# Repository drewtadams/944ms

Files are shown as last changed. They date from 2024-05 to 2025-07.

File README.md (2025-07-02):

# 944ms

The purpose of this guide is to walk through the microsquirt conversion process on an early Porsche 944 with the following goals in mind:

1. utilize as many of the stock parts as possible
2. avoid or minimize the amount of non-bolt-on modifications and fabrication
3. for any part that must be fabricated, try to do so in a way that is easily or readily available (e.g. 3d printing)

**Please read the [DISCLAIMER](disclaimer) before proceeding with any modifications.**

## Sections

 1. [Useful Links](#useful-links)
 2. [Printed Parts](#printed-parts)
 3. [Required Parts](#required-parts)
 4. [Putting it Together](#putting-it-together)

## Useful Links

Though detailed instructions of the entire build can be found in the [Putting it Together](#putting-it-together) section, there are several forums, guides, documentation, and general conversations that were researched and poured over for this project. The information found has proven invaluable and could prove beneficial for other MicroSquirt conversions. They are listed below:

 * [Microsquirt setup/use guide](https://www.useasydocs.com/) (note the [wiring diagram](https://www.useasydocs.com/details/ew3_hires.gif))
 * [General build](https://rennlist.com/forums/924-931-944-951-968-forum/873173-summer-build-thread-megasquirt-and-more-2.html)
 * [General parts overview and tune settings](https://rennlist.com/forums/924-931-944-951-968-forum/831248-a-practical-guide-to-megasquirting-your-944-a.html)
 * [General discussion](https://rennlist.com/forums/924-931-944-951-968-forum/860305-who-is-using-microsquirt-megasquirt.html)
 * Hall sensor on cam: [msextra](https://www.msextra.com/forums/viewtopic.php?t=69564) and [rennlist](https://rennlist.com/forums/944-turbo-and-turbo-s-forum/1088676-fyi-crank-trigger-solution-for-30-no-trigger-wheel-needed.html)
 * [Generic wiring guide](https://rennlist.com/forums/924-931-944-951-968-forum/424355-microsquirt-stand-alone-ecu-installation-guide.html) (particularly useful when used in conjunction with the [speed/reference sensor pinout](https://www.clarks-garage.com/shop-manual/ign-02.htm) for connecting hall sensor to VR-1 or VR-1)
 * [Youtube wiring playlist](https://www.youtube.com/playlist?list=PL6KUN7OA-UQNufmcnJdhSTtK0emy2OQQv)
 * General build checklist: [reddit](https://www.reddit.com/r/megasquirt/comments/3fw4x1/porsche_944_microsquirt_project_completed/) or [msextra](https://www.msextra.com/forums/viewtopic.php?t=59524)
 * TPS alternatives: [951](https://rennlist.com/forums/944-turbo-and-turbo-s-forum/1267168-951-throttle-position-sensor-tps-alternative-solution.html) or [m50](https://rennlist.com/forums/944-turbo-and-turbo-s-forum/968375-what-alternate-tps-units-fit-our-throttle-bodies-2.html)
 * [Alternative VW parts](https://m.me/ch/AbbR2fU9JG5es8ac/)
 * Interchangable parts: [google docs](https://docs.google.com/spreadsheets/d/1jSTkPCnTwhv91jEnysElxuuS8_pDJxy0), [deancent.com](https://www.deancent.com/porsche-944-parts-without-the-premium-price-tag/), or [rennlist](https://rennlist.com/forums/924-931-944-951-968-forum/297421-parts-cross-reference.html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)
 * [DME plug swap](https://rennlist.com/forums/944-and-944s-forum/1266575-microsquirt-ecu-for-porsche-944-s2-motronic-replacement-how-to.html)
 * [Clark's Garage](https://www.clarks-garage.com/) (voltages, current ratings, etc.)

## Printed Parts

All parts were designed to be printed on an Ender 5+ and sliced with Cura. Some adjustments may be necessary depending on the printer and/or slicer, either to the .stl or the printed part itself (e.g. drilling, filing, or sanding down some areas), but general dimensions should be close enough to work. While the links below direct to Thingiverse, the .stl files have also been included under `/printed_parts`.

 * [AFM mods](https://www.thingiverse.com/thing:6618742)
 * [IAT intake tube](https://www.thingiverse.com/thing:6598815)
 * [m50 TPS adapter](https://www.thingiverse.com/thing:6610332)

> Note: the AFM mods and TPS adapter were eventually sent to be machined by a 3rd party service ([SendCutSend](https://sendcutsend.com/)) in 6061 T6 aluminum. While certain plastics likely would have worked well, I opted for a more rigid and heat-tolerant material. They totalled roughly $25.

## Required Parts

The following parts are what were chosen based on price, shipping times, ease of install, or a combination of the aforementioned. Additional parts that were considered but not used are listed [here](#additional-parts-considered). Some parts were purchased in multiples or bulk (e.g. fuses) because it was cheaper or nearly the same price to do so.

It should be noted that the total cost includes taxes and shipping midway through 2024; prices may be different depending on location, availability, and other miscellaneous factors (e.g. inflation, price hikes, etc.).

| Group | Item | Part Number | Price |
|---|---|---|---|
| Cam Sync | [Hall speed sensor](https://www.mouser.com/ProductDetail/ZF/GS100502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) | 540-GS100502 | `$45.05` |
| Cam Sync | [Flanged sleeve bearing](https://www.mcmaster.com/) | 7815K62 | `$12.59` |
| Cam Sync | [M12 x 1.00 tap](https://www.amazon.com/gp/product/B09X7HYMFM) | M12X1.0_Hand_Tap_RH | `$12.87` |
| Cam Sync | [2.4k ohm resistor](https://www.amazon.com/EDGELEC-Resistor-Tolerance-Resistance-Optional/dp/B07HDFRYPK) | B07HDFRYPK | `$5.89` |
| ECU | [MicroSquirt with 8' harness](https://www.diyautotune.com/product/microsquirt-engine-management-system-w-8-foot-wiring-harness/) | MicroSqrt8 | `$390.95` |
| ECU | [18"x8" aluminum sheet metal](https://www.acehardware.com/departments/hardware/metal-sheets-and-rods/sheet-metal/5157615) | 5157615 | `$12.99` |
| ECU | [48-position PDC with Terminal Seals](https://www.kinnettickreations.com/product-page/48-position-pdc) | NA | `$55.00` |
| ECU | [2x 4-pin High Capacity Relay](https://www.kinnettickreations.com/product-page/4-pin-high-capacity-iso-280-relay) | NA | `$10.00` |
| ECU | [Mini fuse kit](https://www.amazon.com/dp/B0D5CZNPQW) | BXS001 | `$5.98` |
| ECU | [36A 6-position terminal block](https://www.amazon.com/dp/B0B24FZWPH) | TB-3506 | `$8.99` |
| Fuel | [4x 33# high-impedance fuel injectors](https://www.ebay.com/itm/266002307469) | 0280150431 | `$96.17` |
| Ignition | [8x Chevy Ignition Coil](https://www.amazon.com/dp/B07FV8C4KJ) (only need 4) | 12611424 | `$89.99` |
| Ignition | [2x LS Ignition Coil Bracket](https://www.amazon.com/dp/B0BBR26F6S) | 12558693 | `$26.99` |
| Intake | [GM IAT open-element sensor](https://www.diyautotune.com/product/gm-open-element-iat-sensor-with-pigtail/) | IATwPiggy | `$24.49` |
| MAP | [GM 1 bar MAP with pigtail](https://www.ebay.com/itm/324792585183) | 12223861 | `$17.17` |
| O2 | [Spartan 2 wideband with LSU 4.9](https://www.14point7.com/products/spartan-lambda-controller-2) (discont. use Spartan 3) | NA | `$125.00` |
| Speed Sensor | [3 pin Bosch EV1 connector](https://www.amazon.com/dp/B0D6Y4Z4FP) | 191972525B | `$11.39` |
| TPS | [m50 TPS](https://www.autozone.com/engine-management/throttle-position-sensor-tps/p/uro-throttle-position-sensor-tps-uro-017795/1323039_0_0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) | 13631721456 | `$55.81` |
| TPS | [2x m3x25 bolt with nut](https://www.amazon.com/gp/product/B0BPFXP2M9) | BXG-M3-400-0012 | `$25.68` |

**Total Parts Cost: `$1,021.61`**

## Additional Parts Considered

The following are parts that were considered but not used. The indices here correlate with those in the [required parts](#required-parts) section above, as does the structure and format, but the cost may or may not include taxes and shipping as they weren't actually purchased. Additional research should be done before purchasing anything listed here to ensure it will work for your application if you choose to alter your route.

 1. Cam sync
    * [hall speed sensor, digikey](https://www.digikey.com/en/products/detail/zf-electronics/GS100502/361998) | GS100502 | `$46.36`
    * [hall speed sensor, diyautotune](https://www.diyautotune.com/product/crankshaft-position-sensor-hall-effect-threaded-body/) | HallThreaded-K | `$102.99`
    * [camshaft trigger kit, clewett](https://www.clewett.com/index.php?main_page=product_info&cPath=59&products_id=306) | 1002-08 | `$195.00`
    * [camshaft trigger kit, lindsey racing](https://www.lindseyracing.com/LR/Porsche/LRA-EM-CAM-ASSY.html) | LRA-EM-CAM | `$475.00`
 2. MAP
    * [GM 1 bar MAP, amazon](https://www.amazon.com/AUTEX-Manifold-Absolute-Pressure-Compatible/dp/B0BB6J8PB2) | 19106672 | `$15.05`
    * [GM 1 bar MAP, clewett](https://www.clewett.com/index.php?main_page=product_info&products_id=80) | 71110 | `$61.00`
 3. [LS2 coil pack](https://thedubshop.com/ls2-coil-pack-set-import/) | IGN_COIL_LS2-IMP-SET
 | `$99.95`
 4. TPS
    * [951, ebay, used](https://www.ebay.com/itm/166226599785) | 280120400 | `$124.99`
    * [951, ebay, new](https://www.ebay.com/itm/362088697124) | 280120400 | `$244.97`
 5. [distributor delete plate](https://www.clewett.com/index.php?main_page=product_info&products_id=309) | 1002-06 | `$56.00`

## Putting it Together

### Cam sync

A general discussion for utilizing a hall effect sensor can be found on [rennlist](https://rennlist.com/forums/944-turbo-and-turbo-s-forum/1088676-fyi-crank-trigger-solution-for-30-no-trigger-wheel-needed.html). The process used here is similar, with the only difference being the orientation of the sleeve bearing.

As opposed to having the flange of the sleeve bearing on the outside of the cam timing belt cover:

 1. grind/sand down the protruding rib on the inside of the cover closest to the inspection hole and one side of the sleeve & flange
 2. press the sleeve bearing into the inspection hole from the inside with a rubber mallet and a large diameter punch or bold head

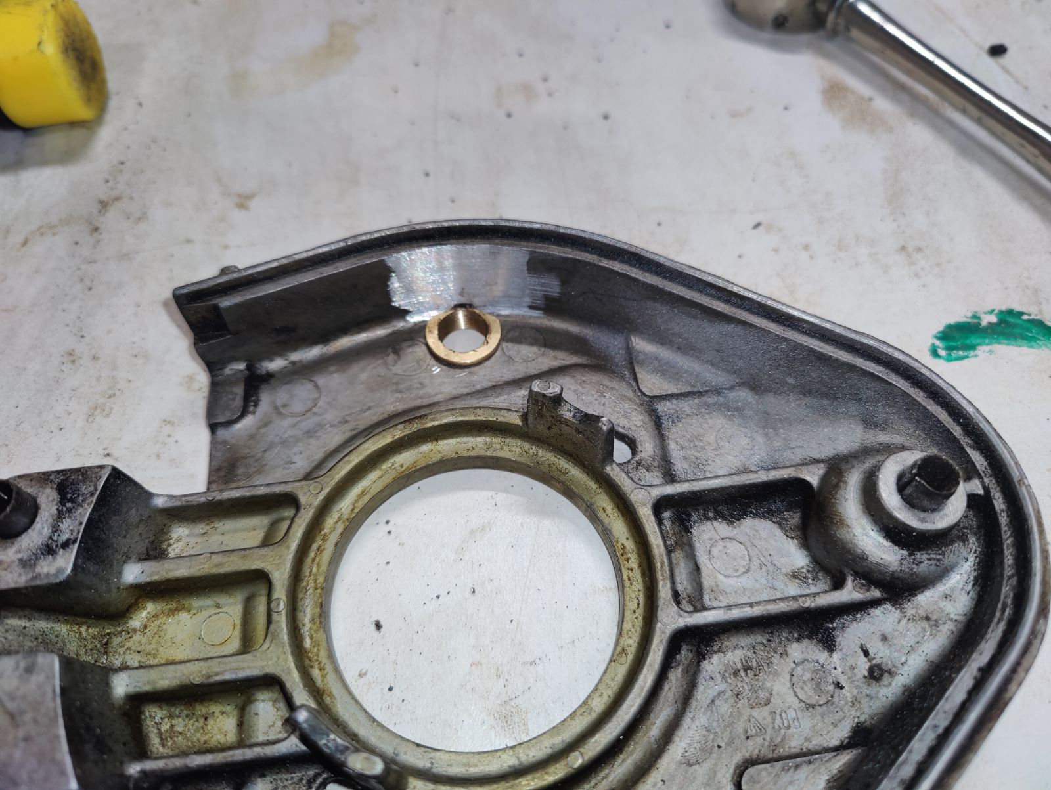
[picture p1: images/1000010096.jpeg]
ground and pressed sleeve bearing


3. grind off the protruding portion of the sleeve from the outside

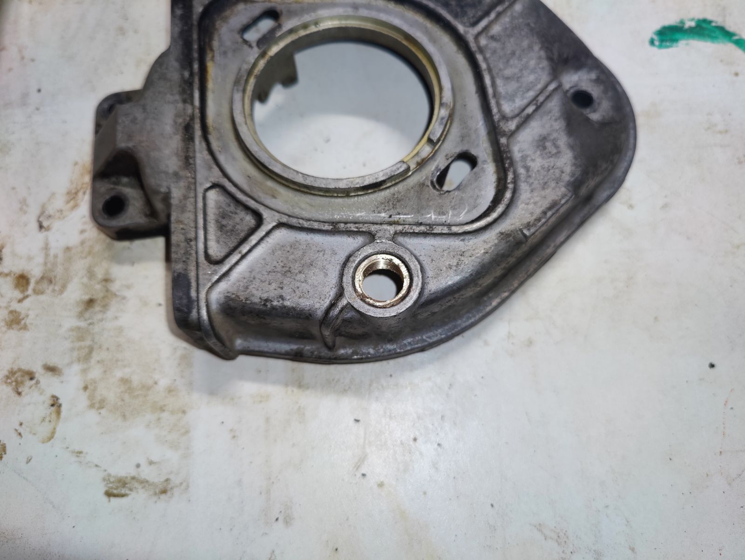
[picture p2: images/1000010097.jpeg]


4. clean up the grind and tap the sleeve with an m12x1mm tap

Once tapped, the hall effect sensor should be able to thread easily into the sleeve bearing. This method uses the flange to keep the sensor from backing out of the cover without relying on adhesives.

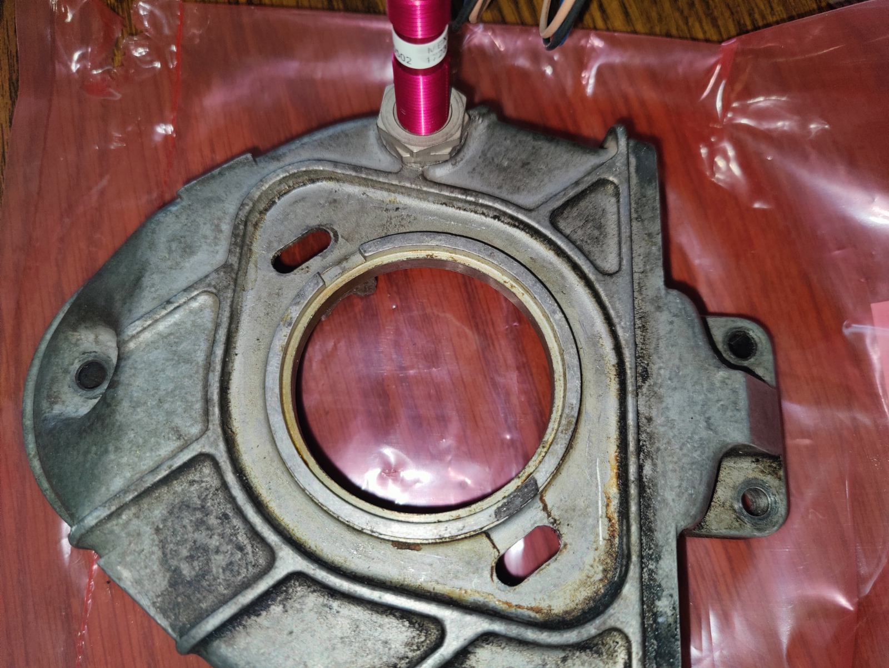
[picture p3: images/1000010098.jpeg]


### AFM modification

For all intents and purposes, the AFM will be used as a glorified intake tube. The gate must be held in the open position to allow full flow of air - this can be done with the [afm gate stop](https://www.thingiverse.com/thing:6618742):

 1. remove the plastic cover on the AFM to reveal its electronics (should pry up - should have some type of silicone or adhesive holding it)

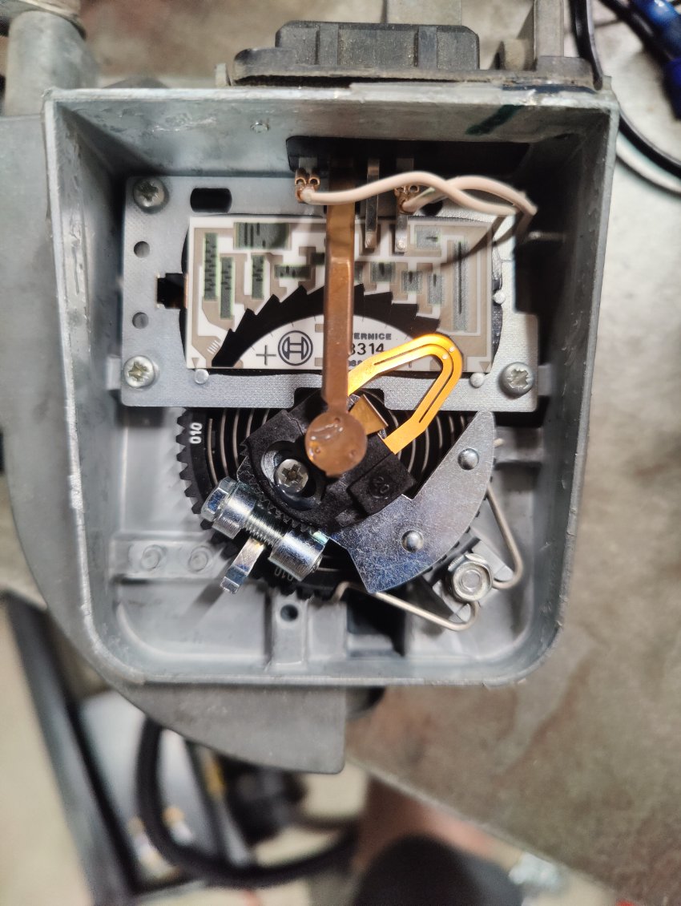
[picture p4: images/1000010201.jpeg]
afm opened
 

 2. unplug both terminals leading to the sensor plug, remove the 4 sensor plug mounting screws (keep track of the screws), and pull the sensor plug out of the case
 
 3. remove the contact wiper arm retaining screw and pull the contact wiper arm out of the case

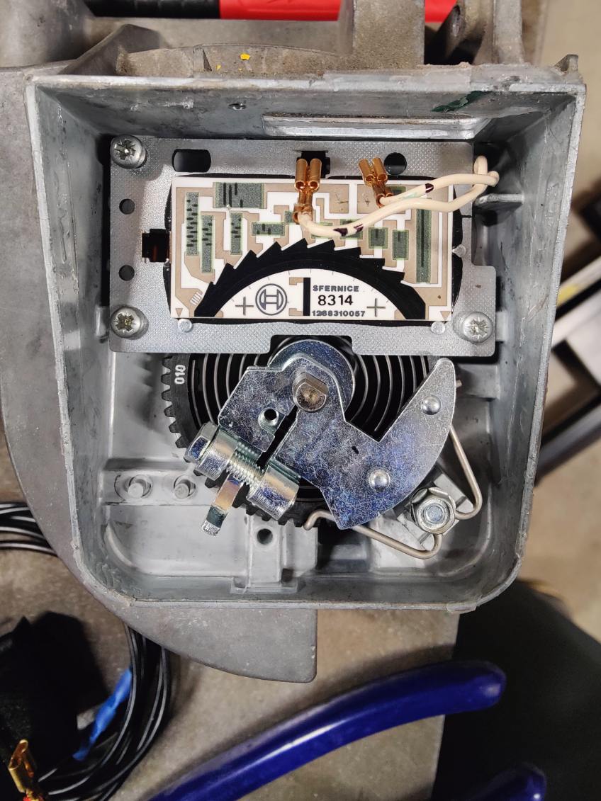
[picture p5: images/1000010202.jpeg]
afm sensor plug removal
 

 4. remove the 3 plate mounting screws holding the resistor board down and remove the resistor board

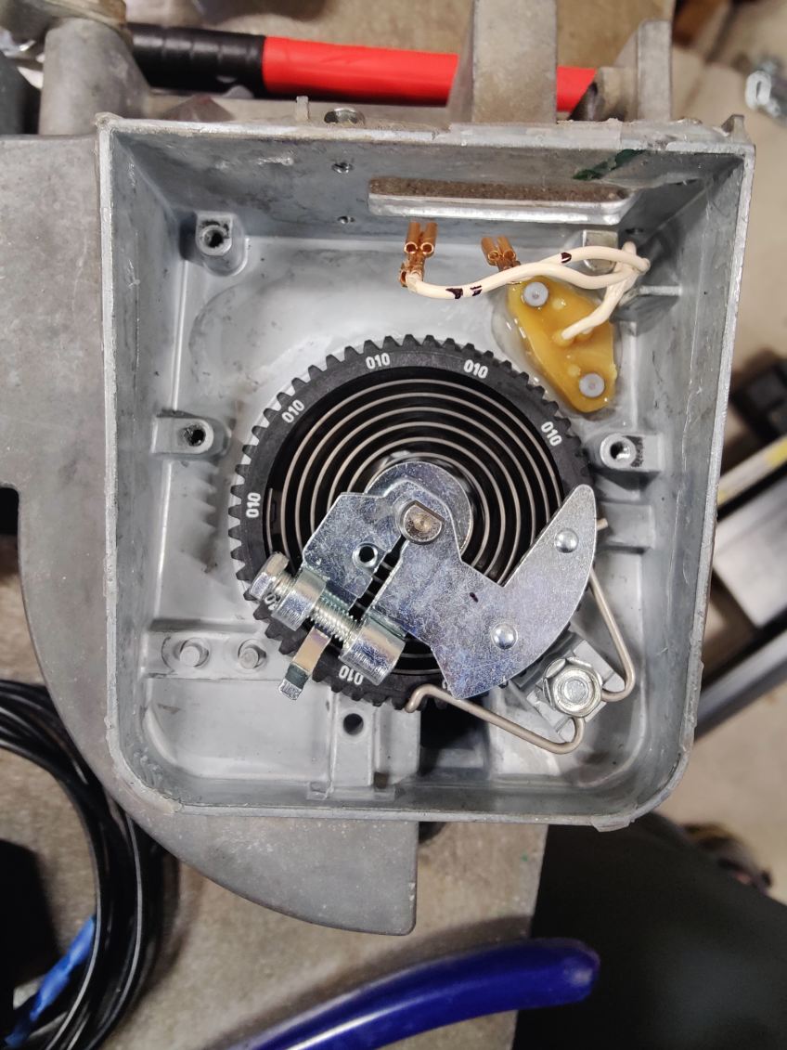
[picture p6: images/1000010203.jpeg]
afm contact board removal
 

 5. remove the clamp bolt and remove the contact mount

 6. remove the bolt holding the spring dial retention clip and remove the retention clip (keep track of the bolt)

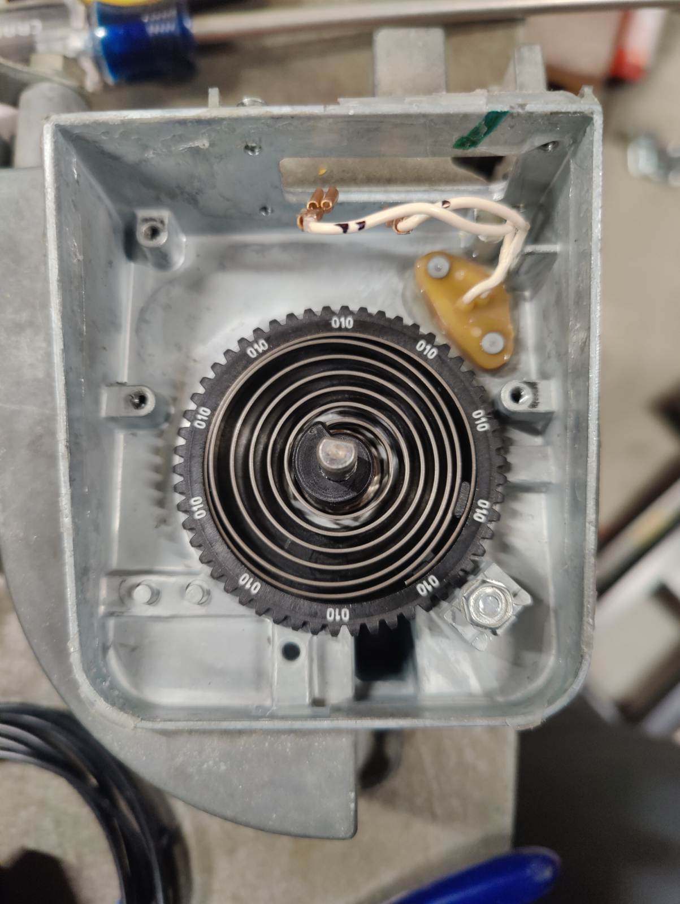
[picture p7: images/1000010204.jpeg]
afm contact and spring dial clip removal
 

 7. slide the spring dial off the gate shaft (it's a tight fit, so a flat-head screwdriver may be necessary)

 8. remove the snap ring (image shows it still in place)

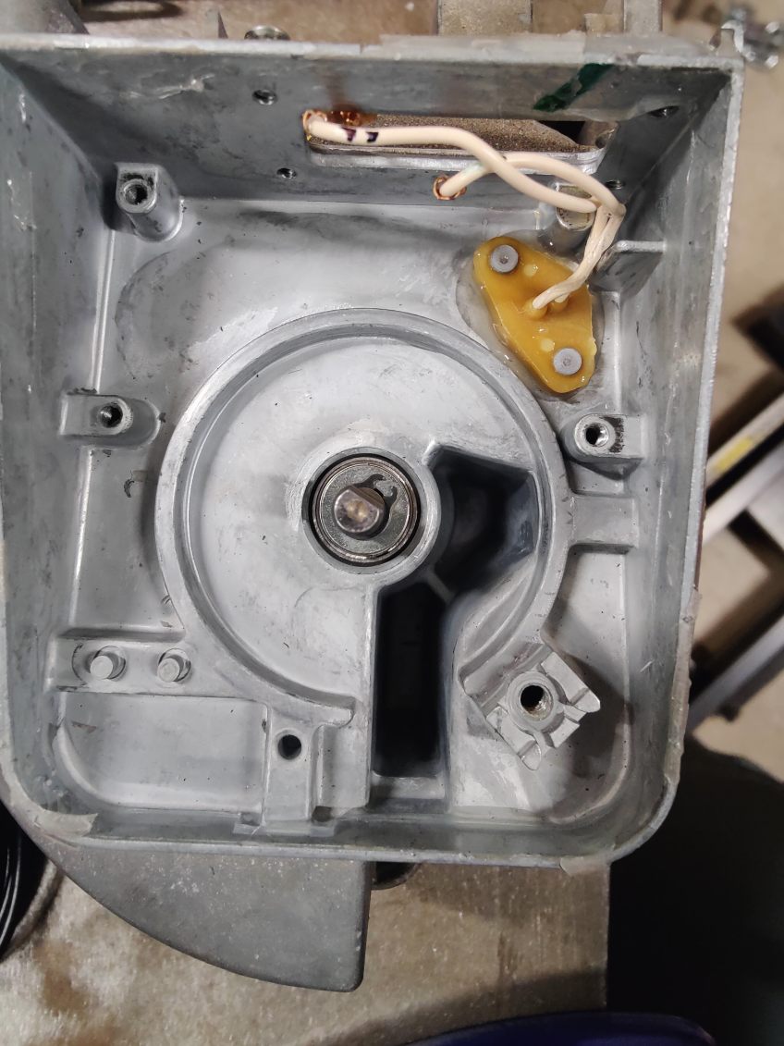
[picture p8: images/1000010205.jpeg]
afm spring dial removal
 

 9. push the air gate open and slide the [afm gate stop](https://www.thingiverse.com/thing:6618742) down the shaft

 10. bolt the gate stop down

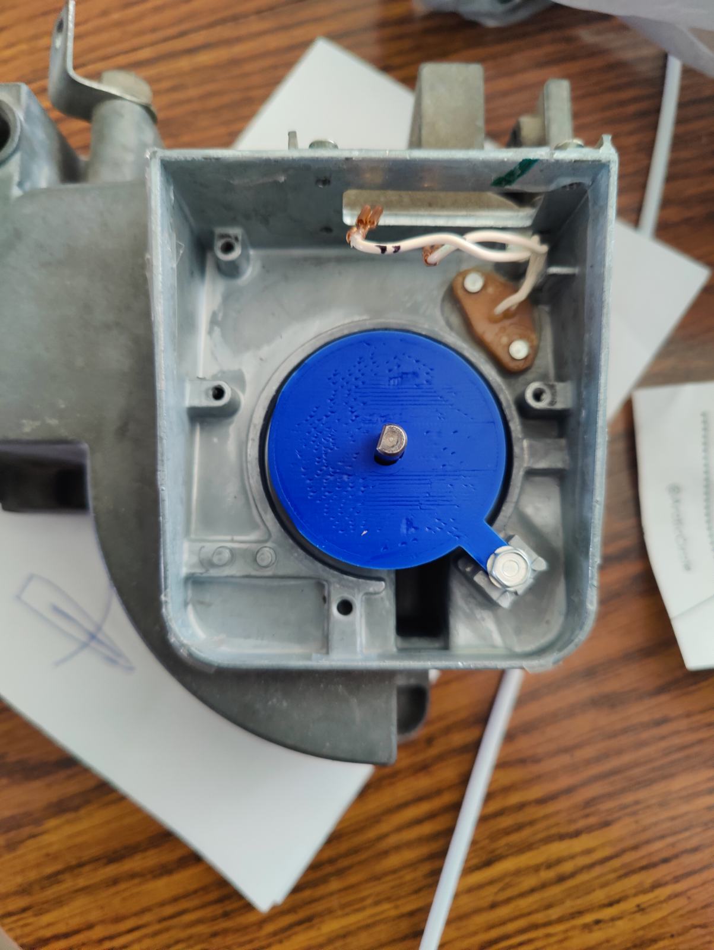
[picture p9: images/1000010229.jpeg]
afm gate stop install
 

 11. attach the [sensor plug block off](https://www.thingiverse.com/thing:6618742) on the outside of where the sensor plug was removed

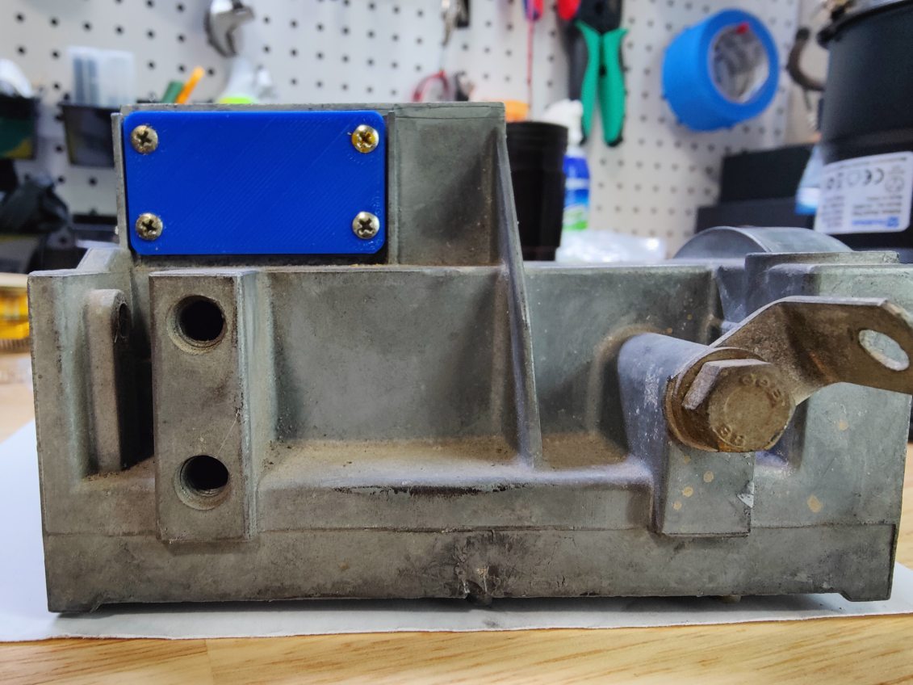
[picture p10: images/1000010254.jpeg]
afm sensor plug block off install
 

>Note: sealing the sensor plug block off isn't necessary due to the use of the MAP sensor

 12. put a thin bead of high-temp silicone along the top walls where the plastic cover sits and press the cover on

### IAT installation

### TPS adapter

### Wiring it up

I followed this diagram published by James Murray on page 15 of the [Microsquirt Hardware Manual](https://www.msextra.com/doc/pdf/html/Microsquirt_Hardware-3.4.pdf/Microsquirt_Hardware-3.4.html):

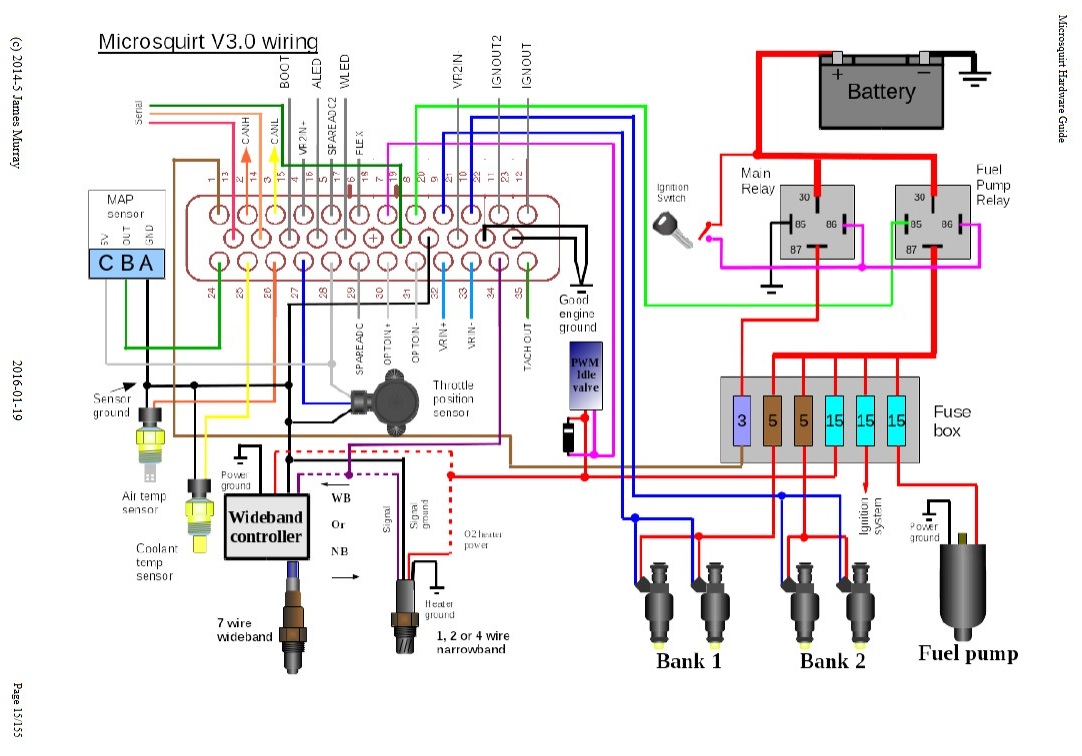
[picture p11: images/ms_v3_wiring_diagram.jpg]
microsquirt v3 wiring diagram


I opted to make a relay board of sorts using the 6-position terminal block and 48-position PDC on an 8" wide aluminum sheet:

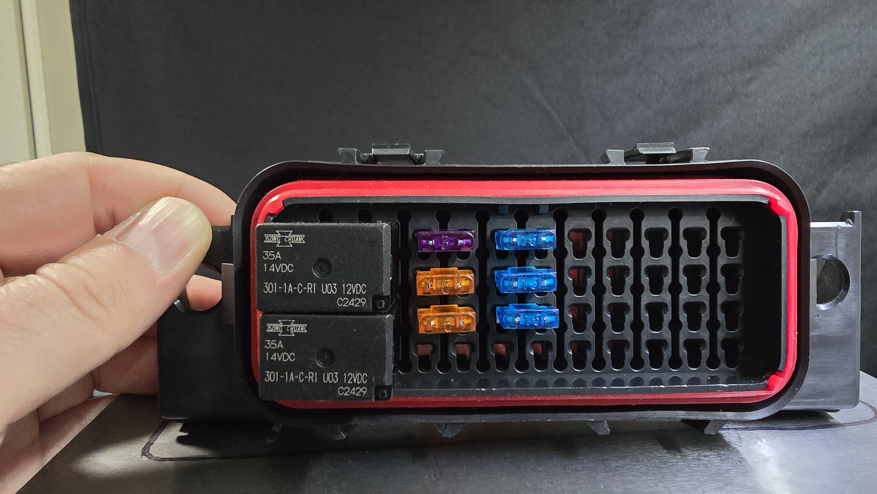
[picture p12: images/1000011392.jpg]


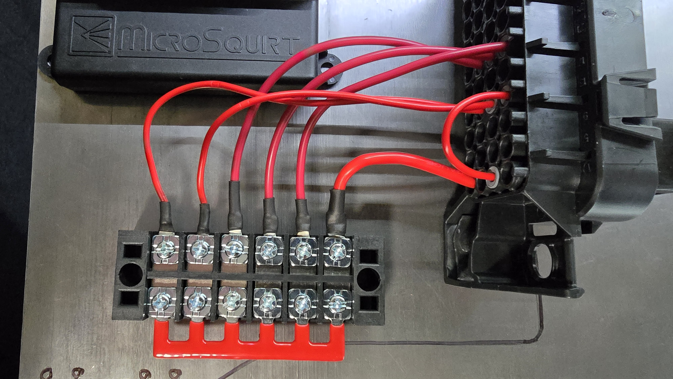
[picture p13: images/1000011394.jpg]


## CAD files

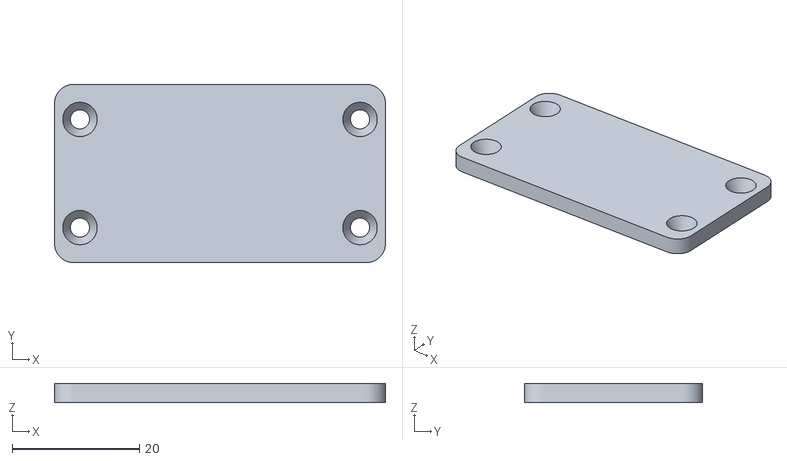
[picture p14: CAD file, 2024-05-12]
printed_parts/afm_sensor_plug_block_off.stl
52.0 x 28.0 x 3.00

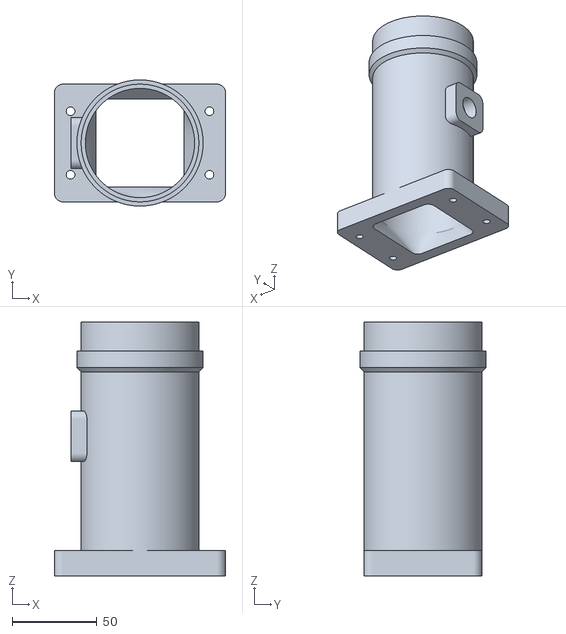
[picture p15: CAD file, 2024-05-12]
printed_parts/iat_intake_tube.stl
101.0 x 74.5 x 150.0

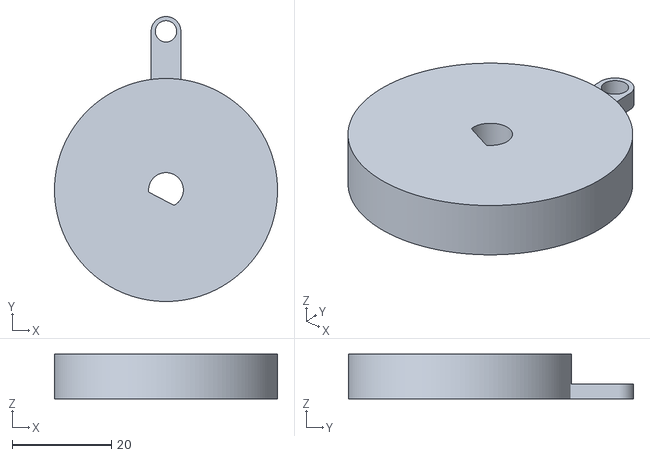
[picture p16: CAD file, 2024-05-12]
printed_parts/afm_gate_stop.stl
45.0 x 57.5 x 9.00

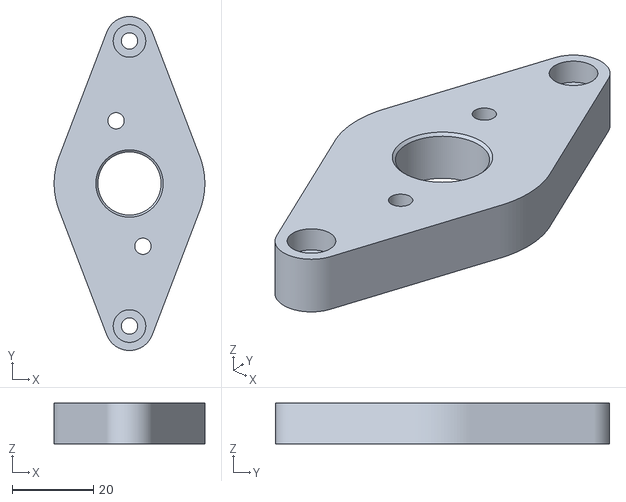
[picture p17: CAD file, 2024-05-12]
printed_parts/m50_tps_adapter.stl
37.0 x 82.0 x 10.0
